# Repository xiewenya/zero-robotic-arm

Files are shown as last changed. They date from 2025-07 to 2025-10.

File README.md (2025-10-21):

# 零一造物_ZERO机械臂
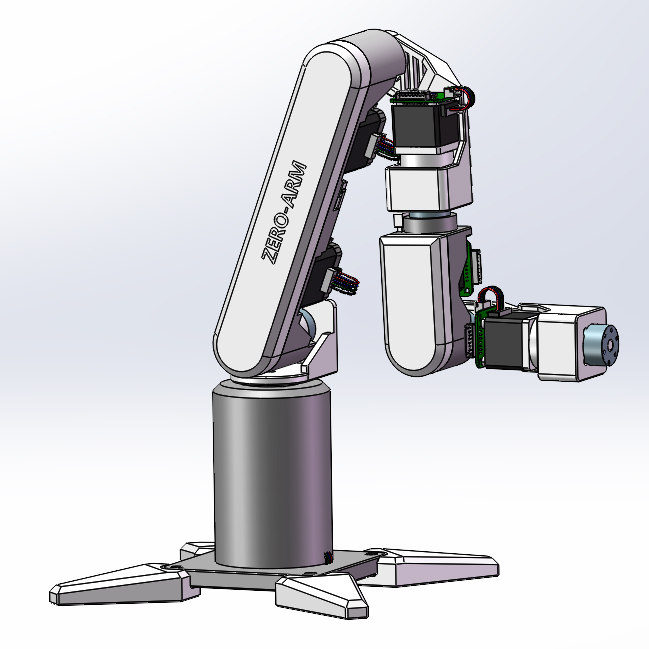
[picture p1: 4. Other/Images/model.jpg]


### 废话
大家好，我是零一造物，很高兴能在这里与大家相遇！说来惭愧，写代码那么多年，还是第一次开源🤦‍♂️，有点小紧张，哈哈哈哈哈。不管怎么样，真心地希望我能给大家带来帮助。

### 介绍
B站: [【开源】为了跟上大佬们的步伐，我决定从零到一做个智能机械臂](https://www.bilibili.com/video/BV1d63Dz7ERN/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)  
小红书：[【开源】为了跟上大佬们的步伐，我决定从零到一做个智能机械臂](https://www.xiaohongshu.com/discovery/item/6868cb63000000002203e9a4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)  
抖音: [【开源】为了跟上大佬们的步伐，我决定从零到一做个智能机械臂](https://v.douyin.com/LI0cadQi1AU/)  
(广告先做起来😄)  

机械臂ZERO是我在机器人领域的第一次探索，这个项目的诞生源于一个简单的愿望——打造一款高性价比、人人都能拥有的桌面级机械臂。我希望通过它，将机器人领域的核心知识串联起来，从基础的结构设计、运动学原理、控制理论，到前沿的强化学习、大模型等方向，逐步构建一个完整的学习体系。  

更重要的是，我想把这段学习旅程分享给所有志同道合的朋友，和大家一起交流想法、碰撞灵感，甚至合作探索更酷的可能性。如果这个项目能为你带来一点点启发或帮助，那将是我最大的快乐！  

让我们一起学习，一起进步，一起从零到一！

本项目计划完成如下功能：
- 机械臂结构设计 (已完成，2025-07-09)
- 机器人运动学逆解 (已完成，2025-07-09)
- PID控制 (已完成，2025-07-09)
- 串口控制 （已完成，2025-07-09）
- 手柄控制 （已完成，2025-07-09）
- MQTT远程控制 
- WEB可视化平台
- 语音识别
- 语音合成
- 大模型接入
- 数据收集及强化学习 （已完成，2025-10-21）
____
### 目录结构
1.  Model: 机械臂三维模型文件
2.  Software:  存放所有代码类文件  
    2.1. robot: 机械臂嵌入式控制代码
3.  Simulink： 运动学仿真模型
4.  BOM: 物料清单
5.  Deep LR: 深度强化学习
____
### 物料清单
所有物料的型号、数量以及购买链接已全部整理到BOM.xlsx中，整个机械臂的物料成本仅需1300左右。
____
### 结构设计
本机械臂结构采用SolidWorks 2022进行三维建模，推荐大家使用同版本的软件，以便获得完整的设计体验。该软件支持运动仿真，且易于二次开发，我还贴心地给大家转了step文件，放在Model/step目录下。
(此外偷懒没有画螺丝，大家用工具量一下孔洞大小和长度自己匹配一下吧😝)

#### 需要3D打印的模型全部集中放在Model/3d_printing_all.3mf中！！！
#### 安装教程详见Model/installation_guide.md！！！
____
### 软件开发
#### 嵌入式软件
机械臂主控芯片采用STM32F407，开发工具为STM32官方两兄弟STM32CubeMX和STM32CubeIDE。
STM32CubeMX用于硬件外设初始化, STM32CubeIDE我一般用来DEBUG和程序下载。敲代码我还是喜欢用VSCode，那两兄弟就是工具人🐶。

核心功能代码包括: 
1. SoftWare/robot/Core/robot.c 机械臂主要控制逻辑  
2. SoftWare/robot/Core/robot_kinematics.c 机械臂运动学逆解算法  
3. SoftWare/robot/Core/robot_cmd.c 机械臂支持的串口/网络命令

关键技术栈包括：
1.  C语言开发
2.  FreeRTOS操作系统
3.  电机与开发板CAN协议通讯
4.  机械臂运动学逆解
5.  PID控制
6.  MQTT网络协议

串口命令

| 命令 | 参数 | 功能 |
| :---: | :---: | :---: |
| rel_rotate  | joint_id angle  | 指定关节的旋转指定角度, 支持负数 |
| hard_reset  | \  | 硬复位：各关节复位, 直到限位开关触发 |
| soft_reset  | \  | 软复位：各关节复位至零点 |
| zero  | \  | 将当前位置设置为零点，软复位将基于当前位置进行复位 |
| auto  | x y z  | 机械臂末端移动到指定位置(x,y,z), 注意坐标方向 |

具体参考：SoftWare/robot/Core/robot_cmd.c的robot_uart1_cmd_table数组定义
____
### 硬件链接
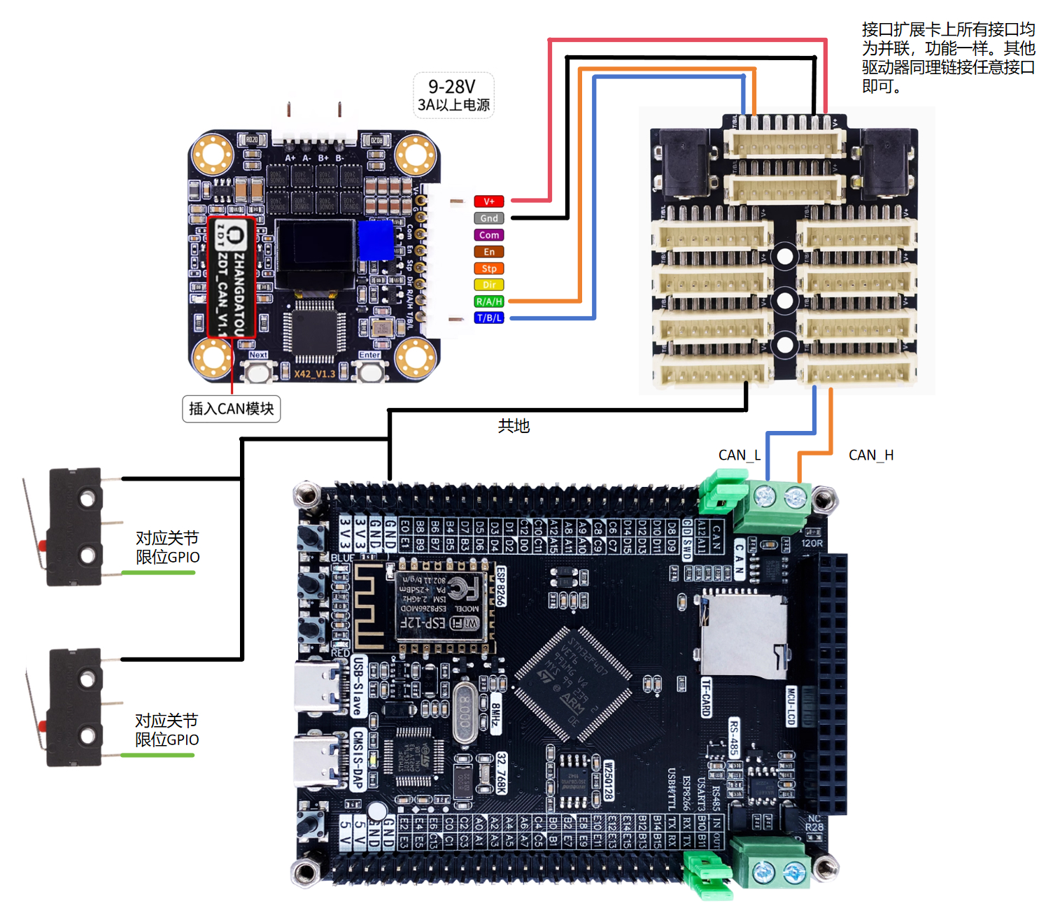
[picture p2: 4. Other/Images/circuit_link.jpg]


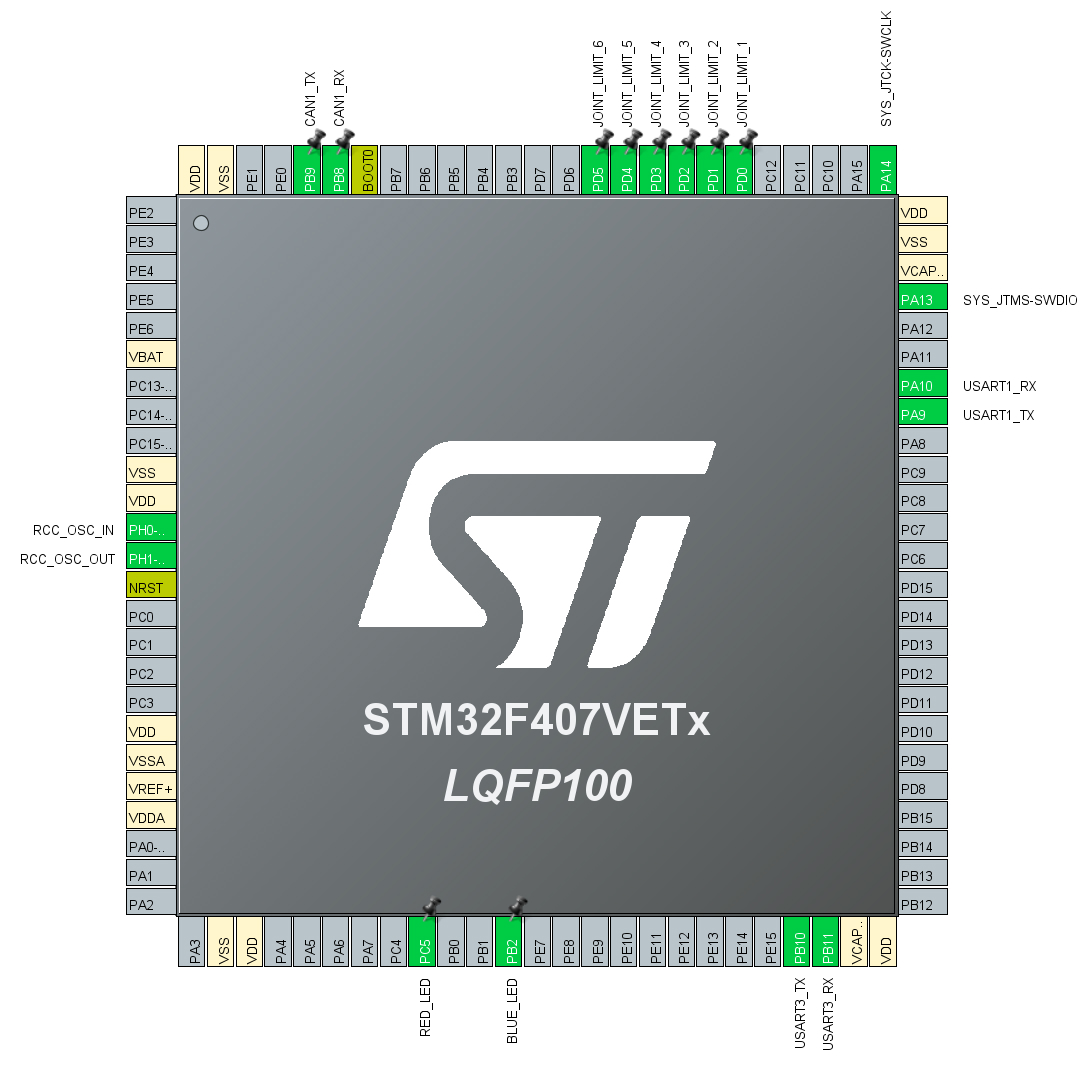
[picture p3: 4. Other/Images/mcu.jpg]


____
### 仿真模型
本项目的运动学逆解推理和仿真验证均使用MATLAB R2023a。
核心文件包括：
1. Simulink/robot_kinematics_sym_v3_0.m 机械臂运动学逆解符号推导过程 
2. Simulink/model_v1.1/URDF_XG_Robot_Arm_Urdf_V1_1 机械臂urdf文件
3. Simulink/URDF_XG_Robot_Arm_Urdf_Control_V3.slx 机械臂运动学逆解simscape仿真验证模型
4. Simulink/robot_run.m URDF_XG_Robot_Arm_Urdf_Control_V3.slx的一键启动脚本
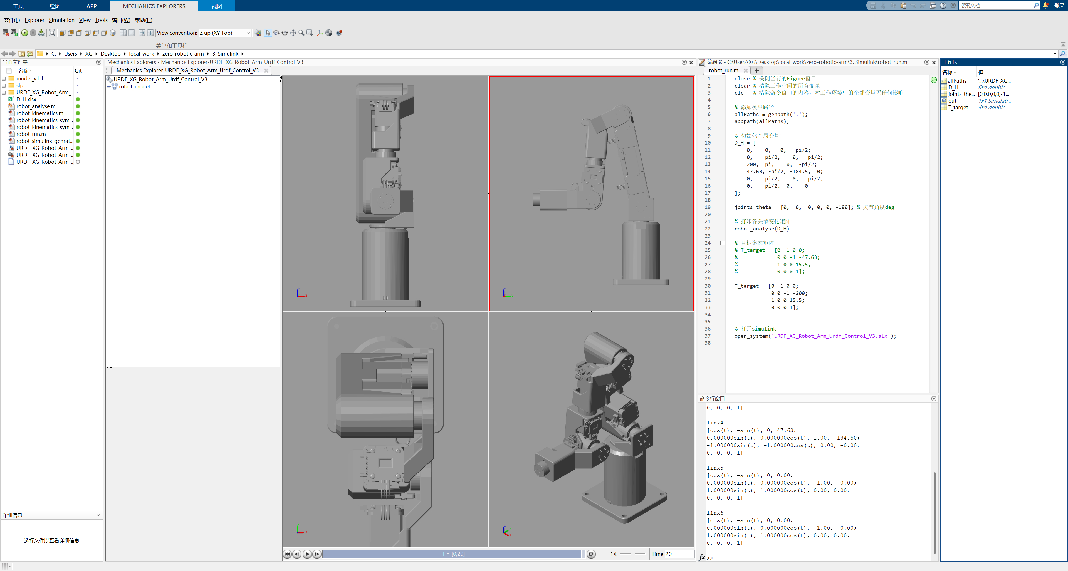
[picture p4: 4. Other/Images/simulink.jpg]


### 深度强化学习
本项目使用了 TD3 深度强化学习算法控制机械臂的末端跟踪随机目标位置。物理仿真环境使用Mujoco, 强化学习框架使用Stable-Baselines3，当然我自己也实现了一个裸写了一个TD3算法，大家可自行参考（没验证过哦~, 但我感觉应该没啥问题, 哈哈哈哈）
核心文件包括：
1. Deep_RL/robot_arm_env.py 环境惩罚规则代码
2. Deep_RL/train_robot_arm.py 训练代码
3. Deep_RL/robot_arm_mujoco.xml mujoco模型定义
4. Deep_RL/mtd3_robot_arm.ipynb 我写的td3算法😄

训练指令：python train_robot_arm.py
测试指令：python train_robot_arm.py --test --model-path ./logs/best_model/best_model.zip --normalize-path ./logs/best_model/vec_normalize.pkl --episodes 50
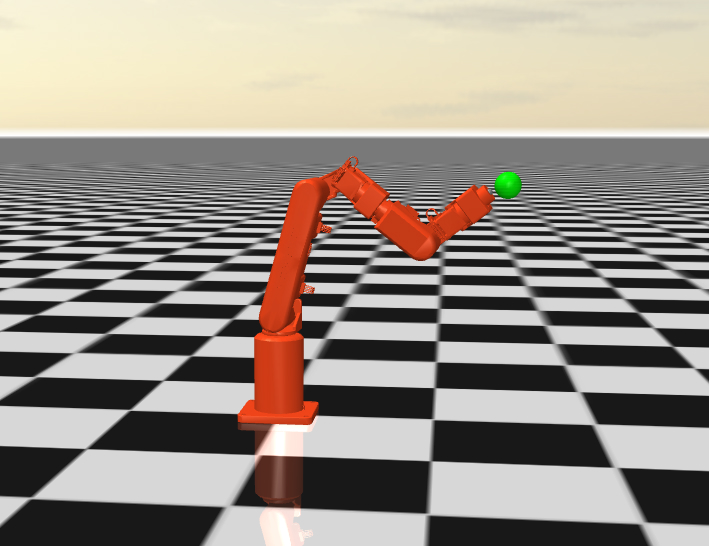
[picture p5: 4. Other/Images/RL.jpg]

____
### 待改进点
1. 行星减速器旷量较大, 存在晃动。（还是买太便宜了😝）
2. 虽然安装了限位开关用于初始位置定位，但上电时系统无法自动判断复位运动方向，导致复位过程存在不确定性。
3. 电路板\电路裸露在外。
4. 存3D打印连接件，在负载场景下，存在刚性不足的问题。

**这一代机械臂主要以学习为主，性价比高，通过它基本能串联起机器人领域的核心知识，当然有诸多待改进的地方，欢迎大家一起找bug，并向我们提交！**   
**下一代机械臂精度和稳定性都做了升级，加入了更多工业级设计，外观也更赛博（当然价格也小幅上升🐶），如果对性能有要求的小伙伴，可以关注我们第二代机械臂ZERO开发计划！**

### 交流群
欢迎大家加入我们的技术交流群！🤖
QQ群：1041684044

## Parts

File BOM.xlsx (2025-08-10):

序号 | 物料名称 | 规格 | 数量 | 备注 | 链接
1 | 行星减速器 | 51：1减速PLZ | 2 |  | https://item.taobao.com/item.htm?id=526104907428
2 | 行星减速器 | 27：1减速 输入6轴径 铣扁1mm | 1 |  | https://item.taobao.com/item.htm?id=526104907428
3 | STM32F407开发板 |  | 1 | 要求芯片为STM32F407，支持CAN协议 | https://item.taobao.com/item.htm?id=681246792404
4 | 42步进电机 | 42-40 身长40 | 2 |  | https://item.taobao.com/item.htm?id=673302946671&skuId=5032954871244
5 | 42行星减速步进电机 | 42HS4013 身长40 减速比50 | 1 |  | https://item.taobao.com/item.htm?id=21034340111&sku_properties=1627207%3A33214301305
6 | 35步进电机 | 35-28 | 1 |  | https://item.taobao.com/item.htm?id=723690490192
7 | 35行星减速步进电机 | 35-26 减速比51 | 2 |  | https://item.taobao.com/item.htm?id=581976167345
8 | 42步进电机驱动器 |  | 3 | 本项目目前仅支持张大头驱动器，需购买CAN协议模块 | https://item.taobao.com/item.htm?id=736578173538
9 | 35步进电机驱动器 |  | 3 | 本项目目前仅支持张大头驱动器，需购买CAN协议模块 | https://item.taobao.com/item.htm?id=736578173538
10 | 圆锥滚子轴承 | 20*37*12 | 1 |  | https://detail.tmall.com/item.htm?id=616787169746
11 | 十字扁平头螺丝 | M3*8 | 32 |  | https://detail.tmall.com/item.htm?id=641493636015
12 | 内六角螺丝圆柱头螺栓 | M5*14 | 4 |  | https://detail.tmall.com/item.htm?id=40189700729
13 | 内六角螺丝圆柱头螺栓 | M4*14 | 4 |  | https://detail.tmall.com/item.htm?id=40189700729
14 | 六角螺帽 | M5 | 4 |  | https://detail.tmall.com/item.htm?detail_redpacket_pop=true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
15 | 六角螺帽 | M3 | 2 |  | https://detail.tmall.com/item.htm?id=549640610734
16 | 土八热熔螺母 | M2*2*3 | 10 |  | https://detail.tmall.com/item.htm?id=809364062256
17 | 3M同步轮 | 3M25齿 孔8 宽11 | 2 |  | https://item.taobao.com/item.htm?id=739009813395
18 | 3M同步轮 | 3M25齿 孔5 宽11 | 3 |  | https://item.taobao.com/item.htm?id=739009813395
19 | 3M同步轮 | 3M25齿 孔6 宽11 | 1 |  | https://item.taobao.com/item.htm?id=739009813395
20 | 3M同步带 | 3M-长171-宽10 | 1 | 任意同步带淘宝店定制即可
21 | 3M同步带 | 3M-长177-宽10 | 2 | 任意同步带淘宝店定制即可
24 | 联轴器 | 外径28mm抱紧式联轴器 孔径8mm | 5 |  | https://detail.tmall.com/item.htm?id=667472622255
25 | 限位开关 | KW11-3Z-A | 3 |  | https://item.taobao.com/item.htm?id=630808292950
26 | 限位开关 | KW11-3Z-B | 2 |  | https://item.taobao.com/item.htm?id=630808292950
27 | 十字扁平头螺丝 | M2*8 | 10 |  | https://detail.tmall.com/item.htm?id=641493636015
28 | 张大头 步进闭环拓展板 |  | 1 |  | https://item.taobao.com/item.htm?ft=t&id=838884896678
29 | 不锈钢圆头螺丝 | M3*28 | 4 | 用来固定驱动器与35行星减速步进电机 | https://detail.tmall.com/item.htm?id=37753866337
30 | 内六角螺丝圆柱头螺栓 | M3*14 | 1 |  | https://detail.tmall.com/item.htm?id=40189700729

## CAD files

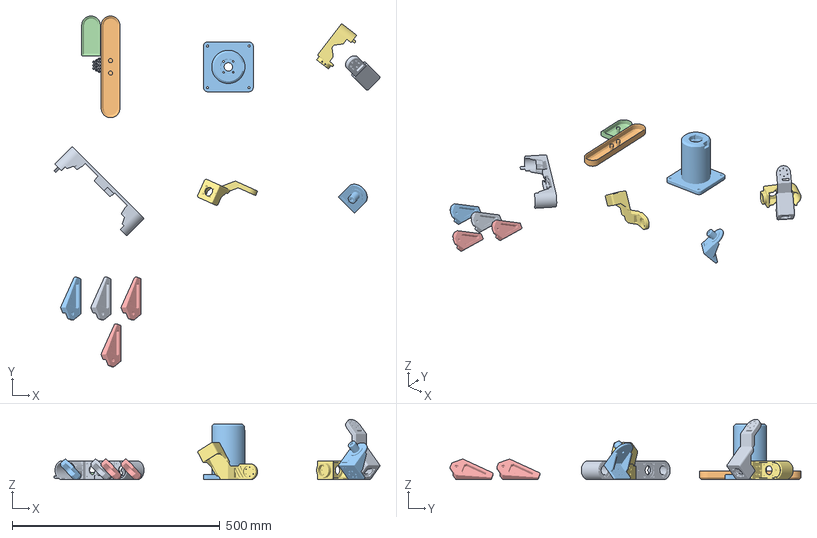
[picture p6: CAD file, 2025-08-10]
1. Model/3d_printing_all.3mf
785.0 x 845.2 x 145.0 mm
frame2.STEP
外壳1.step
frame0^ZERO_ARM.STEP
外壳2.STEP
底座固定爪^XG_Robot_Arm.STEP x 4
1mm垫片.STEP x 12
frame4.STEP
frame3.STEP
frame5.STEP
frame1.STEP

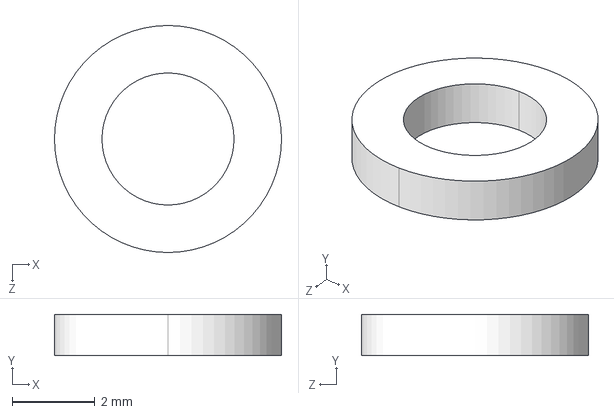
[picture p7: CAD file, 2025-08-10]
1. Model/STEP/1mm垫片.STEP
5.50 x 1.00 x 5.50 mm

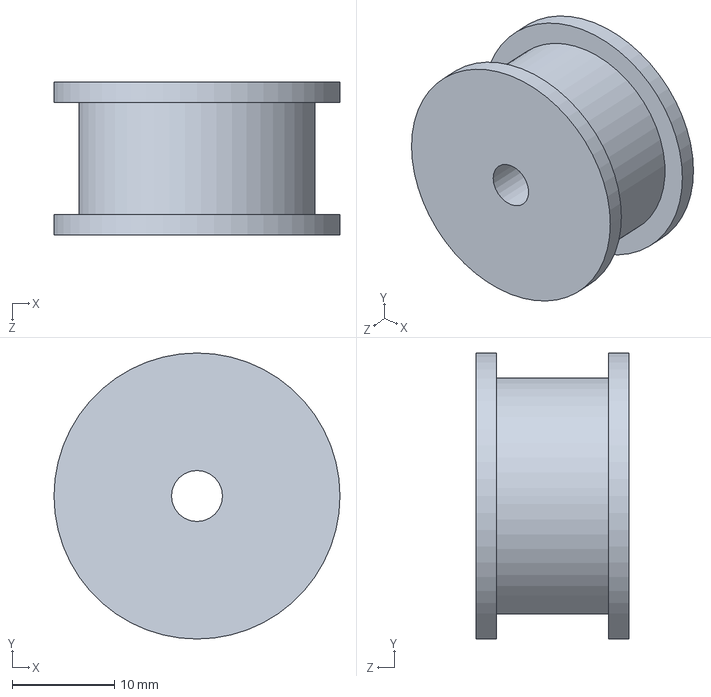
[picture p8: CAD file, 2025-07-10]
3. Simulink/model_v1.1/URDF同步轮M3-05.SLDPRT
28.0 x 28.0 x 15.0 mm

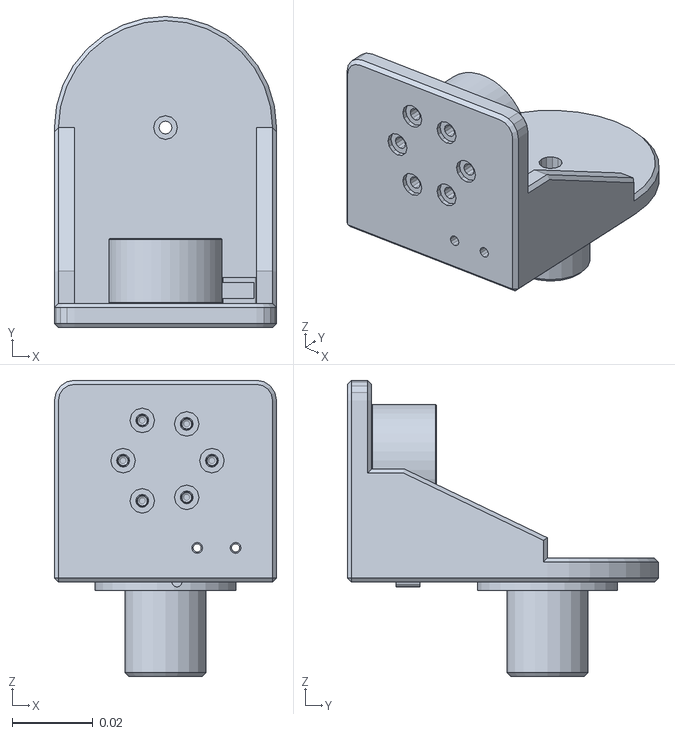
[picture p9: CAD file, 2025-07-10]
5. Deep_LR/meshes/link1.STL
0.055 x 0.077 x 0.0734

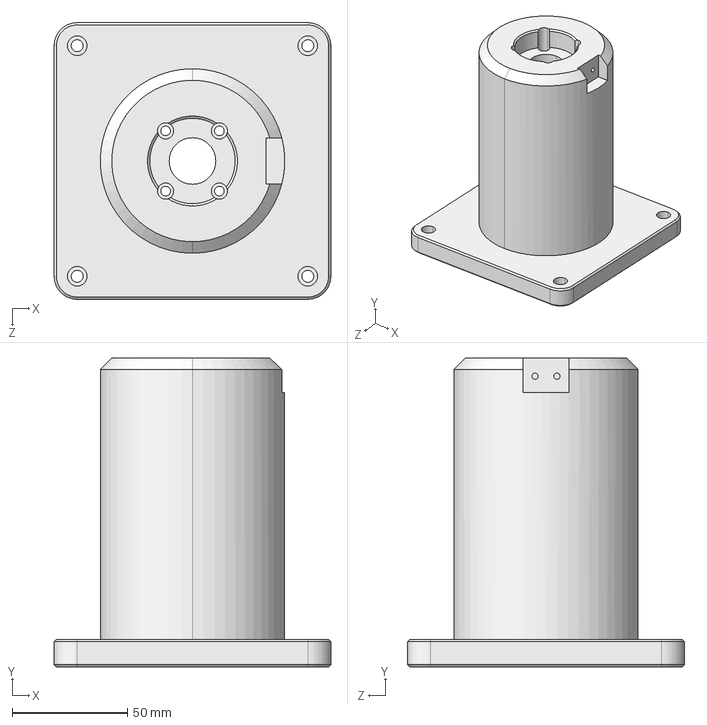
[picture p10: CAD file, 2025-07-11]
1. Model/STEP/frame0^ZERO_ARM.STEP
120.0 x 134.0 x 120.0 mm

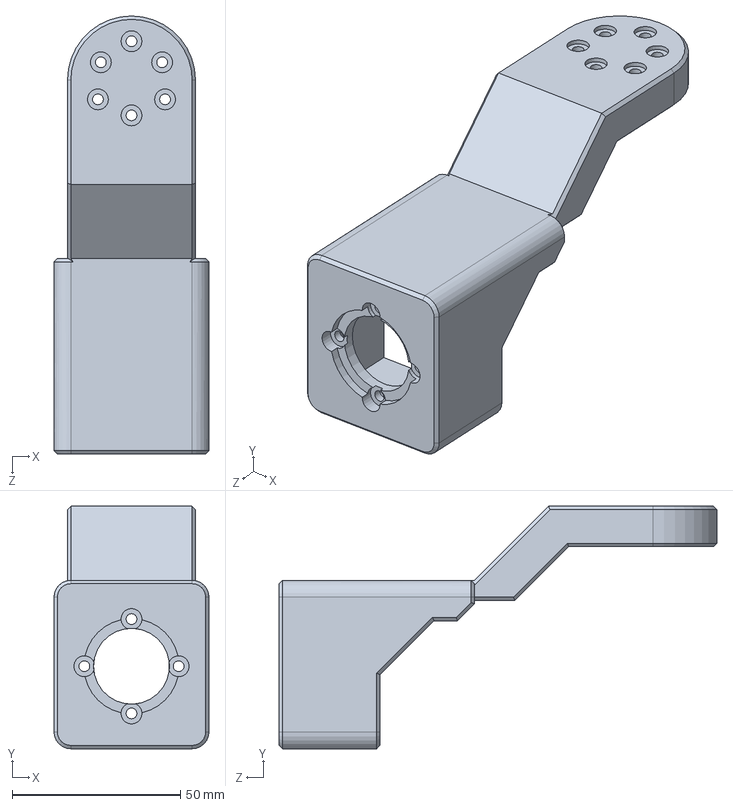
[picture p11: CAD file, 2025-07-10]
3. Simulink/model_v1.1/URDFframe5.SLDPRT
46.0 x 72.0 x 130.0 mm

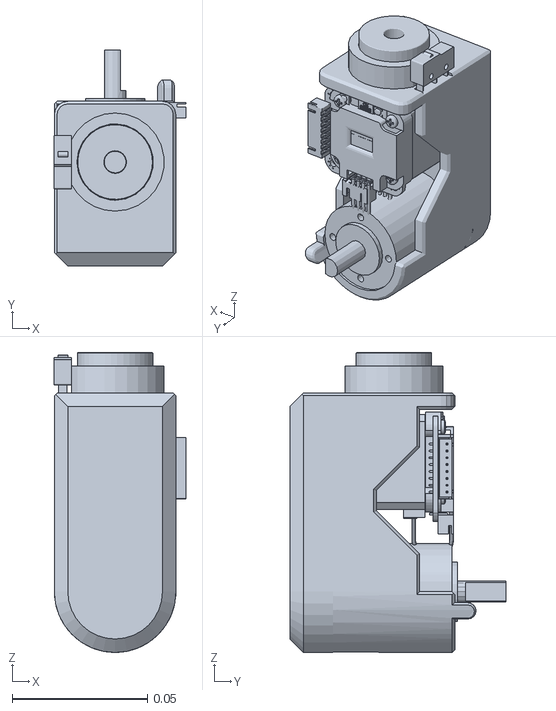
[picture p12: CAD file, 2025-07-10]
5. Deep_LR/meshes/link4.STL
0.0487 x 0.08 x 0.111

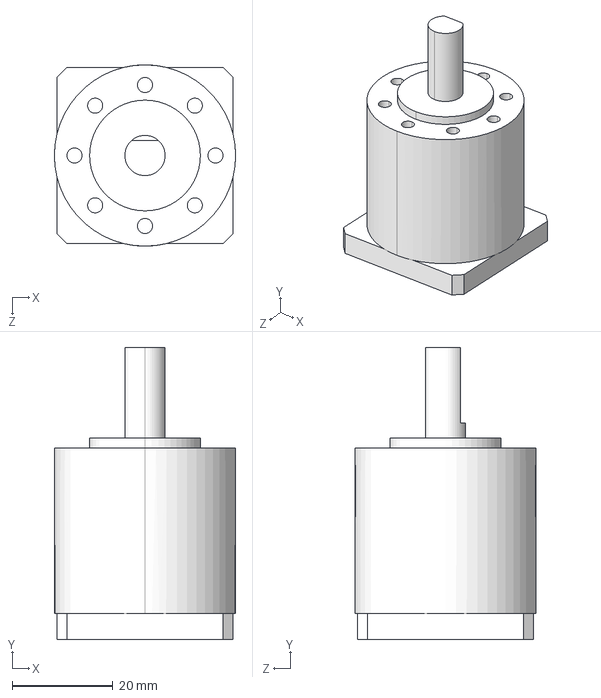
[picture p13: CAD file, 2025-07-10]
1. Model/STEP/单轴行星减速器35-38.step
36.0 x 58.0 x 36.0 mm

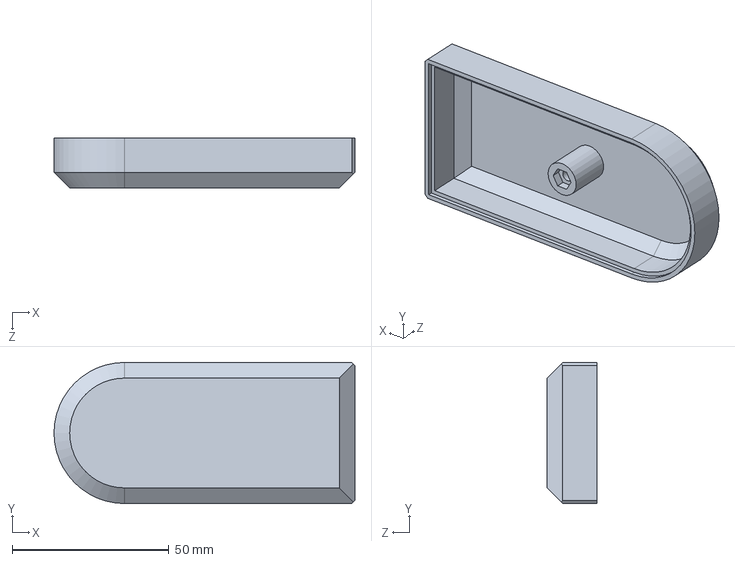
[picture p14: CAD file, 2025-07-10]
3. Simulink/model_v1.1/URDF外壳2.SLDPRT
96.0 x 45.0 x 16.0 mm

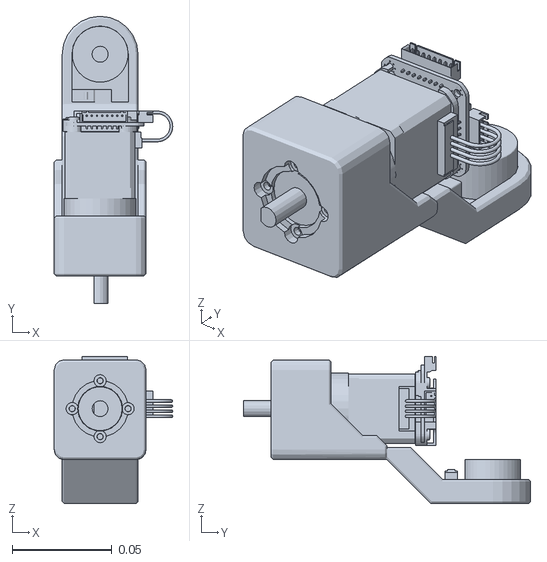
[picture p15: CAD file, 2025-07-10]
5. Deep_LR/meshes/link5.STL
0.0594 x 0.144 x 0.0737

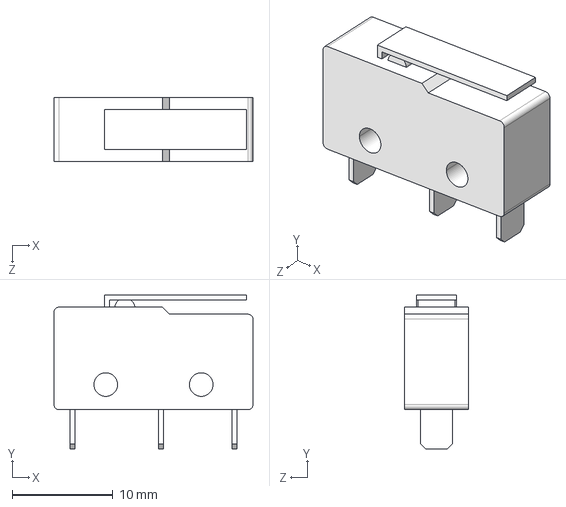
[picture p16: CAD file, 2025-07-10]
1. Model/STEP/限位开关_按下_长柄.step
19.8 x 15.3 x 6.40 mm

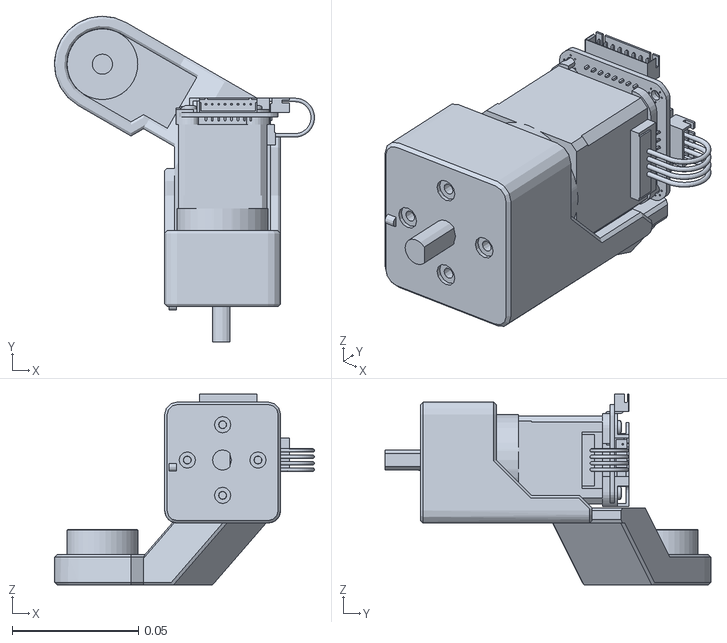
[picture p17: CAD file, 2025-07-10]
5. Deep_LR/meshes/link3.STL
0.103 x 0.129 x 0.0757

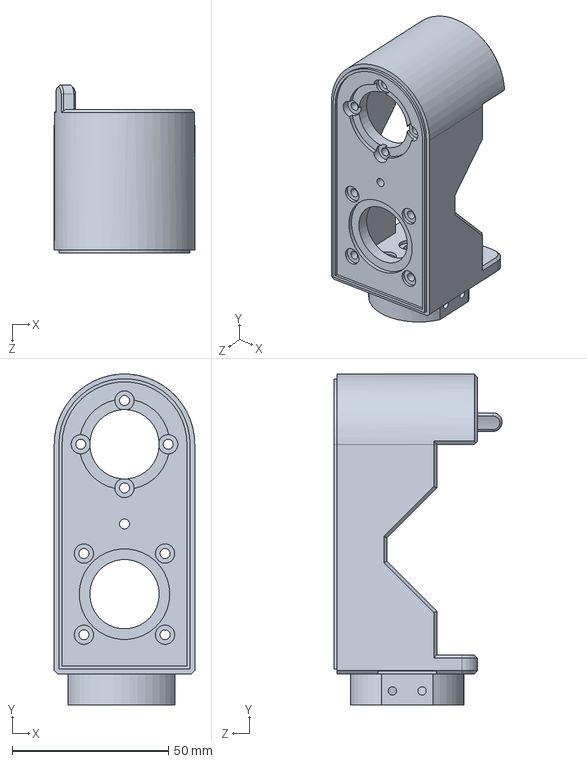
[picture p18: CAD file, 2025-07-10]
3. Simulink/model_v1.1/URDFframe4.SLDPRT
45.0 x 106.0 x 53.9 mm

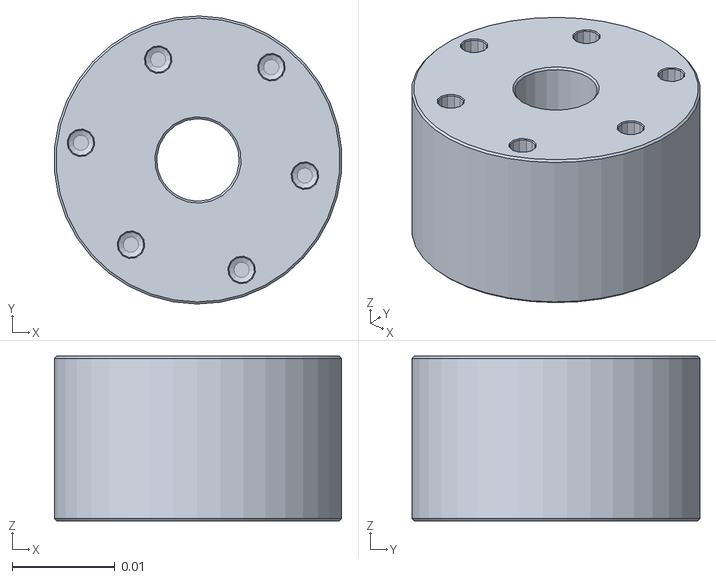
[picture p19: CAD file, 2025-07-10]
5. Deep_LR/meshes/ee_link.STL
0.0279 x 0.028 x 0.016

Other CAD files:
3. Simulink/model_v1.1/URDFZDT_X42_L40Motor.SLDASM
3. Simulink/model_v1.1/URDF42XG二级减速.SLDASM
3. Simulink/model_v1.1/URDF同步轮M3-06.SLDPRT
1. Model/STEP/同步轮M3-06.step
1. Model/42XG二级减速.SLDASM
1. Model/STEP/42XG二级减速.step
1. Model/STEP/ZDT_X35_L28Motor.step
1. Model/STEP/ZDT_X42_L40Motor.step
1. Model/STEP/frame1.step
1. Model/STEP/frame2.step
1. Model/STEP/frame3.step
1. Model/STEP/frame4.step
1. Model/STEP/frame5.step
1. Model/STEP/双轴行星减速器36-38.step
1. Model/STEP/双轴行星减速器36-47.step
1. Model/STEP/同步轮M3-05.step
1. Model/STEP/同步轮M3-08.step
1. Model/STEP/外壳1.step
1. Model/STEP/外壳2.step
1. Model/STEP/底座固定爪.step
1. Model/STEP/手机夹具.step
1. Model/STEP/热熔螺母.step
1. Model/STEP/轴直径8mm_抱紧式联轴器(客户图）.step
1. Model/STEP/限位开关_按下_0.8mm.step
1. Model/ZDT_X35_L28Motor.SLDASM
1. Model/ZDT_X42_L40Motor.SLDASM
1. Model/frame1.SLDPRT
1. Model/frame2.SLDPRT
1. Model/frame3.SLDPRT
1. Model/frame4.SLDPRT
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

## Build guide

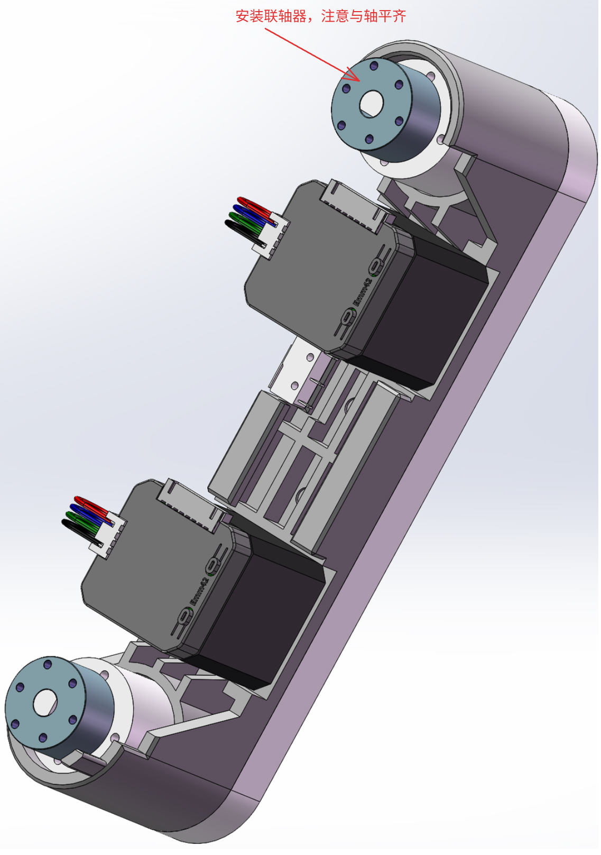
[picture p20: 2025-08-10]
4. Other/Images/install_10.jpg

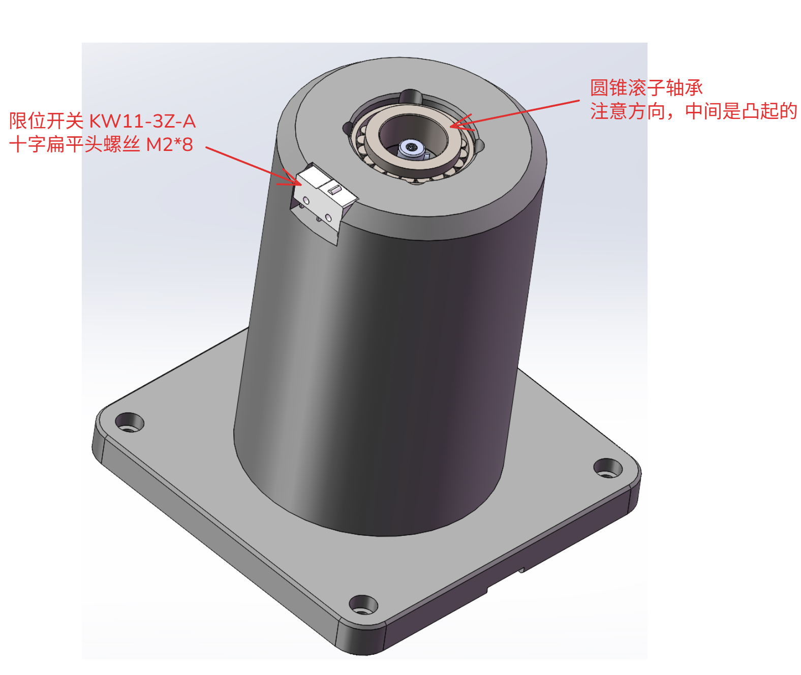
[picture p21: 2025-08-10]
4. Other/Images/install_04.jpg

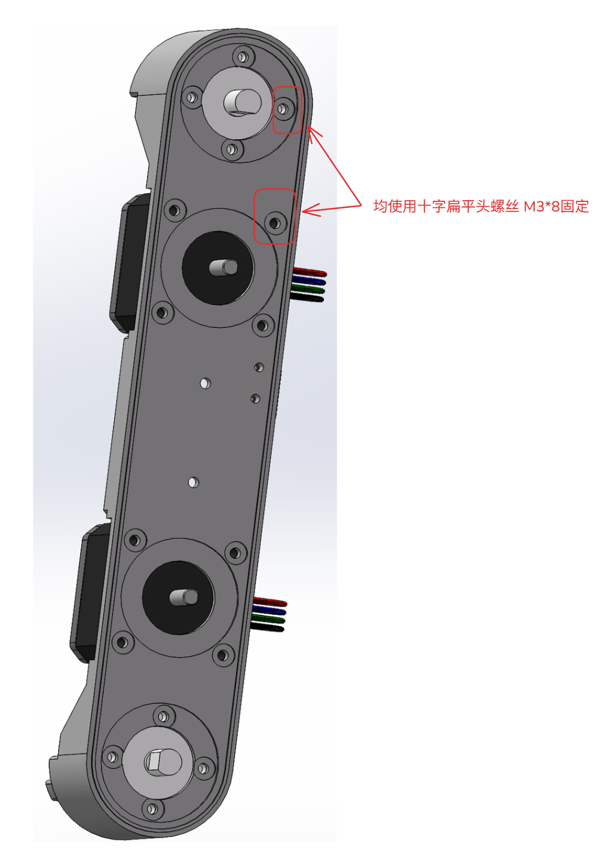
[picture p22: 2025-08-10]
4. Other/Images/install_07.jpg

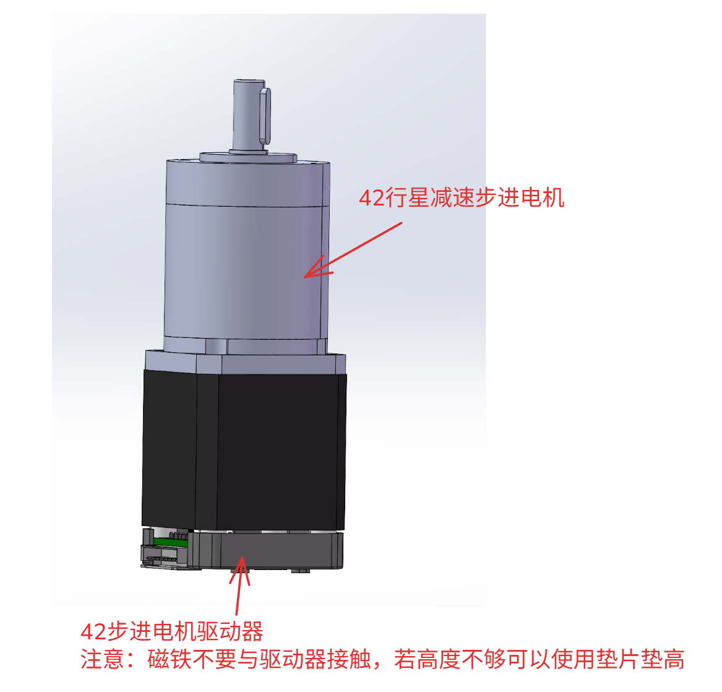
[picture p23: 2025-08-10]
4. Other/Images/install_01.jpg

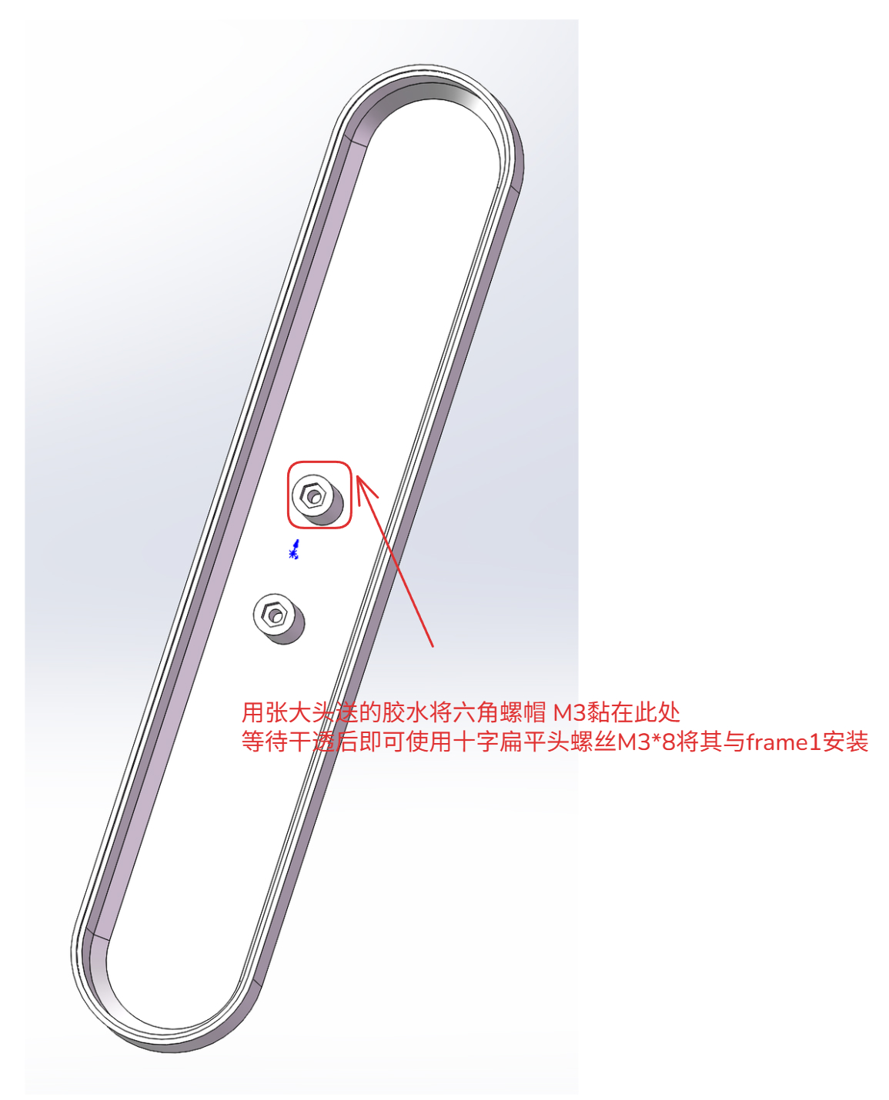
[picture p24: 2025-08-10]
4. Other/Images/install_09.jpg

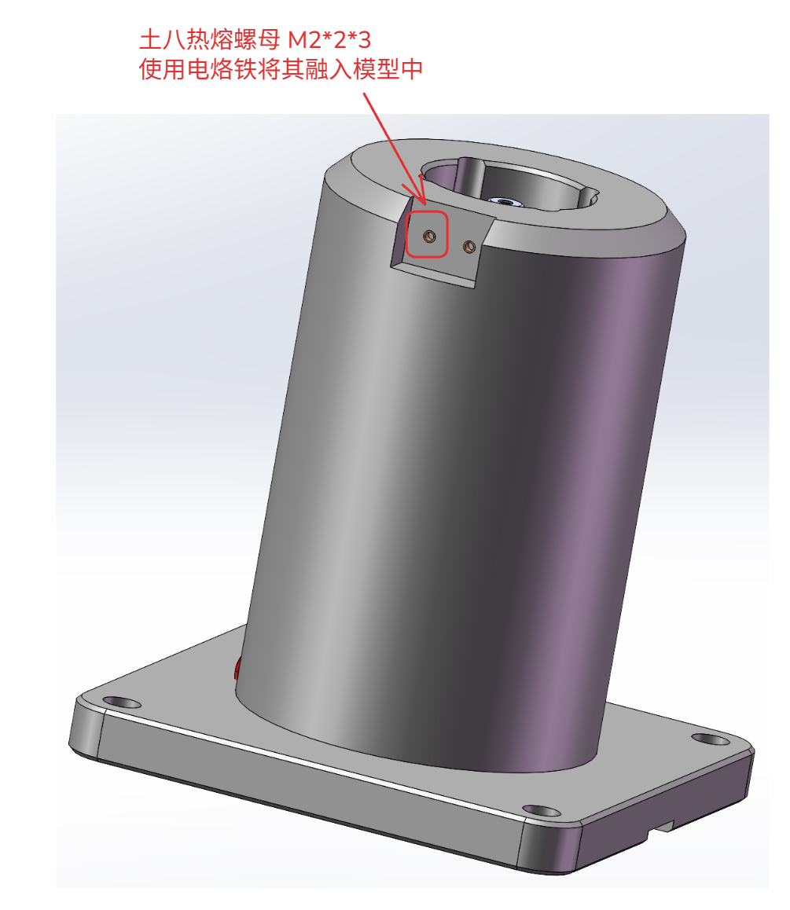
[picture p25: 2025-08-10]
4. Other/Images/install_03.jpg

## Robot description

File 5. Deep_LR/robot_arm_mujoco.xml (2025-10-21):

<mujoco model="URDF_XG_Robot_Arm_Urdf_V1_1">
  <default>
    <default class="robot">
      <default class="motor">
        <joint damping="0.1"/>
        <position forcerange="-20 20"/>
      </default>
      <default class="visual">
        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
      </default>
      <default class="collision">
        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
        <equality solimp="0.99 0.999 1e-05" solref="0.005 1" />
      </default>
    </default>
  </default>

  <compiler angle="radian" />

  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

  <worldbody>
    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
    <light directional="true" ambient=".3 .3 .3" pos="30 30 30" dir="0 -.5 -1" diffuse=".5 .5 .5" specular=".5 .5 .5" />
    <body name="base_link" pos="0.00000000 0.00000000 0.00000000" quat="1 0 0 0" childclass="robot">
      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
      <body name="link1" pos="0 0 0.166" quat="0.7071054825112363 0.0 0.0 0.7071080798594735">
        <joint name="joint1" type="hinge" ref="0.0" class="motor" axis="0 0 1" />
        <inertial pos="0.000159015425944007 -0.0243405579392273 -0.0177069078146256" quat="1.0 0.0 0.0 0.0" mass="0.0608469523040024" diaginertia="3.70074391646153e-05 2.56788832154839e-05 3.87763473470933e-05" />
        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
        <body name="link2" pos="0 0 0" quat="0.4999981633974483 0.49999999999662686 -0.49999999999662686 0.5000018366025516">
          <joint name="joint2" type="hinge" ref="0.0" class="motor" range="-1.5708 1.5708" axis="0 0 1" />
          <inertial pos="0.100016791971952 0.00010706633715631 -0.0107835162525267" quat="1.0 0.0 0.0 0.0" mass="0.433546101825407" diaginertia="0.000140434169717076 0.00105045835658617 0.00104172634579532" />
          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
          <body name="link3" pos="0.2 0 0" quat="-2.5973434669646147e-06 -0.707105482506466 -0.7071080798547033 -2.597353007557415e-06">
            <joint name="joint3" type="hinge" ref="0.0" class="motor" range="0 3.1416" axis="0 0 1" />
            <inertial pos="0.0413167215618623 -0.0479933927735263 -0.0109451750096955" quat="1.0 0.0 0.0 0.0" mass="0.163443679549629" diaginertia="0.000132142857401717 7.6101137062348e-05 0.000133520429120215" />
            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
            <body name="link4" pos="0.047631 -0.1845 0" quat="0.7071054825112363 -0.7071080798594735 0.0 0.0">
              <joint name="joint4" type="hinge" ref="0.0" class="motor" axis="0 0 1" />
              <inertial pos="-2.8160808468243E-05 -0.00682767077230628 0.0299455082197141" quat="1.0 0.0 0.0 0.0" mass="0.178465854809275" diaginertia="0.00010542070955742 0.000111293192127703 4.4231117465552e-05" />
              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
              <body name="link5" pos="0 0 0" quat="0.4999981633974483 0.49999999999662686 -0.49999999999662686 0.5000018366025516">
                <joint name="joint5" type="hinge" ref="0.0" class="motor" range="-1.5708 0" axis="0 0 1" />
                <inertial pos="0.000156431818420899 -0.0617917966301206 -0.0100252833788212" quat="1.0 0.0 0.0 0.0" mass="0.15793222447205" diaginertia="0.000135933655838788 5.60082572905534e-05 0.000121456700565665" />
                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
                <body name="ee_link" pos="0 -0.125 0" quat="0.7071054825112363 0.7071080798594735 0.0 0.0">
                  <joint name="joint6" type="hinge" ref="0.0" class="motor" axis="0 0 1" />
                  <inertial pos="0 5.0666E-17 -0.0081069" quat="1.0 0.0 0.0 0.0" mass="0.0088164" diaginertia="6.5293e-07 6.5293e-07 9.3068e-07" />
                  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
                  <camera name="ee_camera" pos="0 0 0" quat="0 0.707 0.707 0" fovy="60" />
                  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
                </body>
              </body>
            </body>
          </body>
        </body>
      </body>
      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
      <camera name="front_camera" mode="track" fovy="90.0" quat="4.329780281177467e-17 4.329780281177466e-17 0.7071067811865475 0.7071067811865476" pos="0.0 2.0 0.5" />
      <camera name="side_camera" mode="track" fovy="90.0" quat="-0.5 -0.4999999999999999 0.5 0.5000000000000001" pos="-2.0 0.0 0.5" />
    </body>
  </worldbody>

  <actuator>
    <motor name="joint1_ctrl" joint="joint1" class="motor" gear="1" />
    <motor name="joint2_ctrl" joint="joint2" class="motor" gear="1" />
    <motor name="joint3_ctrl" joint="joint3" class="motor" gear="1" />
    <motor name="joint4_ctrl" joint="joint4" class="motor" gear="1" />
    <motor name="joint5_ctrl" joint="joint5" class="motor" gear="1" />
    <motor name="joint6_ctrl" joint="joint6" class="motor" gear="1" />
  </actuator>

  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

  <sensor>
    <framepos name="base_link_site_pos" objtype="site" objname="base_link_site" />
    <framequat name="base_link_site_quat" objtype="site" objname="base_link_site" />
    <framelinvel name="base_link_site_linvel" objtype="site" objname="base_link_site" />
    <frameangvel name="base_link_site_angvel" objtype="site" objname="base_link_site" />
    <velocimeter name="base_link_site_vel" site="base_link_site" />
    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
    <framepos name="ee_site_pos" objtype="site" objname="ee_site" />
    <framelinvel name="ee_site_linvel" objtype="site" objname="ee_site" />
    <frameangvel name="ee_site_angvel" objtype="site" objname="ee_site" />
    <velocimeter name="ee_site_vel" site="ee_site" />
  </sensor>
</mujoco>

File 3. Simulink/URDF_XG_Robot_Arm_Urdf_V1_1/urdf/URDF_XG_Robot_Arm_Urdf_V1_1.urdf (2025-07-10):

<?xml version="1.0" encoding="utf-8"?>
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
<robot name="URDF_XG_Robot_Arm_Urdf_V1_1">
  <link name="base_link">
    <inertial>
      <origin xyz="-6.62271790898662E-05 -0.000162301184482969 0.0589260607237122" rpy="0 0 0" />
      <mass value="0.553880194517112" />
      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
    </inertial>
    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
  </link>
  <link name="link1">
    <inertial>
      <origin xyz="0.000159015425944007 -0.0243405579392273 -0.0177069078146256" rpy="0 0 0" />
      <mass value="0.0608469523040024" />
      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
    </inertial>
    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
  </link>
  <joint name="joint1" type="continuous">
    <origin xyz="0 0 0.166" rpy="0 0 1.5708" />
    <parent link="base_link" />
    <child link="link1" />
    <axis xyz="0 0 1" />
  </joint>
  <link name="link2">
    <inertial>
      <origin xyz="0.100016791971952 0.00010706633715631 -0.0107835162525267" rpy="0 0 0" />
      <mass value="0.433546101825407" />
      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
    </inertial>
    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
  </link>
  <joint name="joint2" type="revolute">
    <origin xyz="0 0 0" rpy="1.5708 -1.5708 0" />
    <parent link="link1" />
    <child link="link2" />
    <axis xyz="0 0 1" />
    <limit lower="-1.5708" upper="1.5708" effort="0" velocity="0" />
  </joint>
  <link name="link3">
    <inertial>
      <origin xyz="0.0413167215618623 -0.0479933927735263 -0.0109451750096955" rpy="0 0 0" />
      <mass value="0.163443679549629" />
      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
    </inertial>
    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
  </link>
  <joint name="joint3" type="revolute">
    <origin xyz="0.2 0 0" rpy="-3.1416 0 1.5708" />
    <parent link="link2" />
    <child link="link3" />
    <axis xyz="0 0 1" />
    <limit lower="0" upper="3.1416" effort="0" velocity="0" />
  </joint>
  <link name="link4">
    <inertial>
      <origin xyz="-2.8160808468243E-05 -0.00682767077230628 0.0299455082197141" rpy="0 0 0" />
      <mass value="0.178465854809275" />
      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
    </inertial>
    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
  </link>
  <joint name="joint4" type="continuous">
    <origin xyz="0.047631 -0.1845 0" rpy="-1.5708 0 0" />
    <parent link="link3" />
    <child link="link4" />
    <axis xyz="0 0 1" />
  </joint>
  <link name="link5">
    <inertial>
      <origin xyz="0.000156431818420899 -0.0617917966301206 -0.0100252833788212" rpy="0 0 0" />
      <mass value="0.15793222447205" />
      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
    </inertial>
    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
  </link>
  <joint name="joint5" type="revolute">
    <origin xyz="0 0 0" rpy="1.5708 -1.5708 0" />
    <parent link="link4" />
    <child link="link5" />
    <axis xyz="0 0 1" />
    <limit lower="-1.5708" upper="0" effort="0" velocity="0" />
  </joint>
  <link name="ee_link">
    <inertial>
      <origin xyz="0 5.0666E-17 -0.0081069" rpy="0 0 0" />
      <mass value="0.0088164" />
      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
    </inertial>
    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
  </link>
  <joint name="joint6" type="continuous">
    <origin xyz="0 -0.125 0" rpy="1.5708 0 0" />
    <parent link="link5" />
    <child link="ee_link" />
    <axis xyz="0 0 1" />
  </joint>
</robot>

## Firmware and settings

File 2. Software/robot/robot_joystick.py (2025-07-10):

import pygame
import serial
import time
import argparse

def send_and_receive_joystick_data(port, baudrate):
    # 初始化pygame和手柄
    pygame.init()
    pygame.joystick.init()
    # 创建一个 Pygame 显示窗口
    screen = pygame.display.set_mode((600, 200))
    pygame.display.set_caption("Joystick Control")

    # 设置字体和文字内容
    font = pygame.font.Font(None, 36)
    text = font.render("Robot joystick is running, press Q to exit", True, (255, 255, 255))
    text_rect = text.get_rect(center=(screen.get_width() / 2, screen.get_height() / 2))

    # 检查是否有手柄连接
    if pygame.joystick.get_count() == 0:
        print("No joystick connected!")
        pygame.quit()
        return

    # 获取第一个手柄
    joystick = pygame.joystick.Joystick(0)
    joystick.init()

    # 打开指定的串口
    ser = None  # 初始化串口对象
    try:
        ser = serial.Serial(port, baudrate, timeout=1)
        print(f"Serial port {port} opened successfully at baudrate {baudrate}.")
        # 发送remote enable命令
        ser.write(b"remote_enable\n")
        time.sleep(3)
    except serial.SerialException as e:
        print(f"Failed to open serial port {port}: {e}")
        pygame.quit()
        return

    # 定义一个函数来获取手柄的axes状态
    def get_joystick_axes():
        pygame.event.pump()  # 处理pygame事件队列
        # 获取所有轴的值，并保留小数点后两位
        axes = [round(joystick.get_axis(i), 2) for i in range(joystick.get_numaxes())]
        return axes

    # 主循环
    try:
        while True:
            axes = get_joystick_axes()
            # 将axes状态转换为指定格式的字符串
            # 格式为：remote_event 0.0 -0.0 0.0 -0.0 -1.0 -1.0
            axes_str = "remote_event " + " ".join(map(str, axes)) + "\n"
            # 发送状态到串口
            ser.write(axes_str.encode())
            # print(f"Sent to {port}: {axes_str.strip()}")

            # 接收串口返回的数据
            if ser.in_waiting > 0:
                received_data = ser.readline().decode().strip()
                print(f"Received from {port}: {received_data}")

            # 处理键盘事件
            for event in pygame.event.get():
                if event.type == pygame.KEYDOWN:
                    if event.key == pygame.K_q:  # 检测 Q 键是否被按下
                        if ser and ser.is_open:
                            ser.write(b"remote_disable\n")
                        pygame.quit()
                        return

            # 填充背景色
            screen.fill((0, 0, 0))
            # 将文字绘制到屏幕上
            screen.blit(text, text_rect)
            # 等待100ms
            time.sleep(0.1)
            # 更新显示
            pygame.display.flip()
    finally:
        # 关闭串口和pygame
        if ser and ser.is_open:
            ser.close()
        pygame.quit()

if __name__ == "__main__":
    # 创建命令行参数解析器
    parser = argparse.ArgumentParser(description="Send joystick data to a serial port and receive data back.")
    parser.add_argument("-p", "--port", type=str, default="COM3", help="Serial port (default: COM3)")
    parser.add_argument("-b", "--baudrate", type=int, default=115200, help="Baudrate (default: 115200)")

    # 解析命令行参数
    args = parser.parse_args()

    # 调用函数
    send_and_receive_joystick_data(args.port, args.baudrate)

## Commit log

2025-07-08 Upload software, model, simulation, and BOM.
    [42XG二级减速.SLDASM, 42XG二级减速.step, BOM.xlsx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]
2025-07-09 add readme
    [BOM.xlsx, URDF42XG二级减速.SLDASM, URDFZDT_X42_L40Motor.SLDASM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]
2025-07-10 修改readme
2025-07-11 Modify the BOM table and add frame0.step
    [BOM.xlsx, frame0^ZERO_ARM.STEP]
2025-08-03 support mqtt control Signed-off-by: XG. <857439011@qq.com>
    [BOM.xlsx]
2025-08-04 bugfix of BOM
    [BOM.xlsx]
2025-08-06 add 3d_printing_all.3mf file
    [3d_printing_all.3mf, BOM.xlsx]
2025-08-10 niu ma trace for yolov
2025-08-10 installation guide
    [3d_printing_all.3mf, BOM.xlsx]
2025-08-10 Revert "installation guide"
    This reverts commit 67423fc8bd85f26400cbacb419dce893ebe79bd0.
    [3d_printing_all.3mf, BOM.xlsx]
2025-08-10 Revert "niu ma trace for yolov"
    This reverts commit 98436f731db6d475c743035a7dd9c1589566e2eb.
2025-10-21 support TD3 LR
    [ee_link.STL, link1.STL, link3.STL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]
